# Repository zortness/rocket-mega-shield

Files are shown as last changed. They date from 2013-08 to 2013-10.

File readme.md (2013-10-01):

Rocket Mega Shield Revision 2
=============================

rendering
rendering
rendering

These are the Eagle files for an Arduino Mega shield with sensors and features needed by aviation and rocketry enthusiasts. 
The board is also designed to be extremely easy to use for any hobbyist application. 

These files are released under the [Creative Commons Attribution-ShareAlike](http://creativecommons.org/licenses/by-sa/3.0/) license. 
You're free to use and modify them for any purpose, including commercial.

These files make use of footprints taken from the [Adafruit Eagle Library](https://github.com/adafruit/Adafruit-Eagle-Library) 
and [Sparkfun Eagle Libraries](https://github.com/sparkfun/SparkFun-Eagle-Libraries). 

My library of modified parts is [available here](https://github.com/zortness/zort-eagle-library).

Concept
--------
This shield is geared toward aviation purposes, specifically rocketry. The board itself does not dictate how it is used.
It can also be used for things like planes, boats, cars, or robotics, though this might be overkill for those purposes.

Features
--------
* Supports 5V and 3.3V boards (Mega or Due)
* Supports MicroSD cards that can operate in SPI mode
* Supports all XBee models, using UART Serial for communication
* -- User selectable XBee on UART0 or UART1 via switch
* -- Tie-down holes included in layout
* 10Hz GPS tied to UART2
* -- External GPS Antenna u.FL connector
* High Sensitivity BMP180 Altimeter (barometric pressure and temperature)
* Full 9-degrees-of-freedom capabilities
* -- 3-Axis 16G accelerometer and magnometer (LSM303DLHCTR)
* -- 3-Axis 8-gauss gyroscope (L3GD20TR)
* 3-Axis 200G accelerometer for high-force calculations (ADXL377)
* External reverse-polarity-protected power supply via JST2 connector
* -- Will also power the Arduino
* -- Can also be powered by the Arduino over USB
* -- Up to 18V
* Input voltage measuring at ~1:6 scale
* 4x high-amp MOSFETs with continuity detection
* -- Designed for rocket deployment pyrotechnics
* Automatic level-shifting for sensors (up to 5V)
* Buzzer for making loud noises
* -- MOSFET controlled, attached to PWM pin 8
* Lots of pretty flashing lights

See the [Bill of Materials](https://github.com/zortness/rocket-mega-shield/blob/master/bom.md)
and [parts manifest](https://github.com/zortness/rocket-mega-shield/blob/master/manifest.txt)
for more information.

Versions
--------
* RocketMega Revision 2.1 - Third prototype, only pin and routing changes from R2 for Due compatability
* RocketMega Revision 2 - Second prototype board, intended for wider production, August 2013
* RocketDuino Revision 1 - Initial prototype board, June 2013 

Prototype Images
----------------
Revision 2

R2

Revision 1

R1_a
R1_b

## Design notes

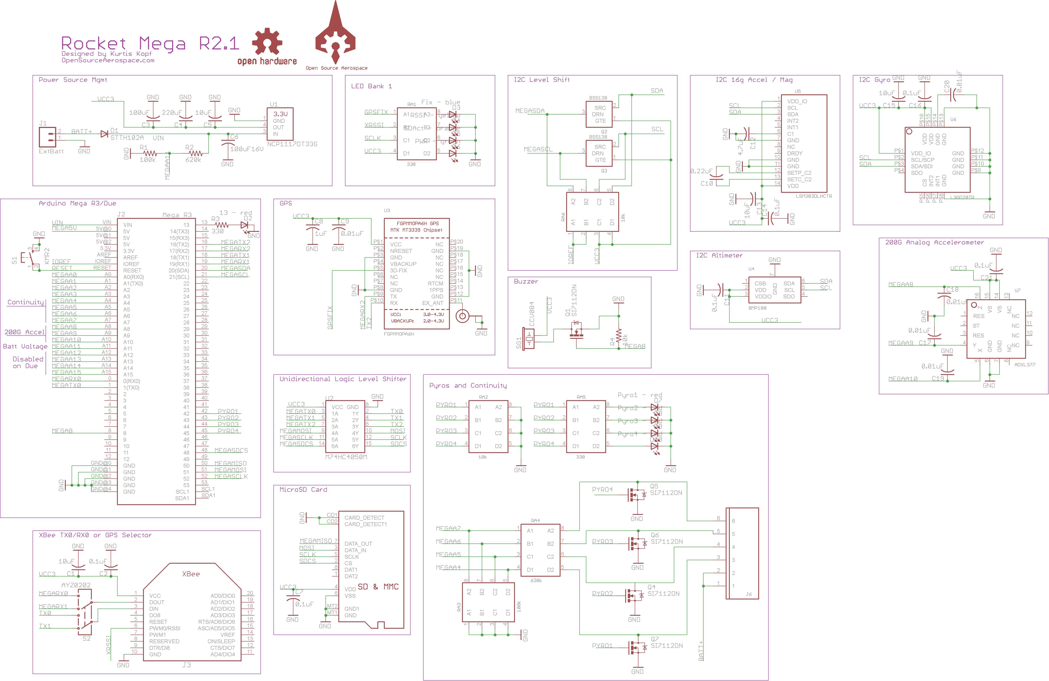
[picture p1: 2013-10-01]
render/rev2.1/schematic.png

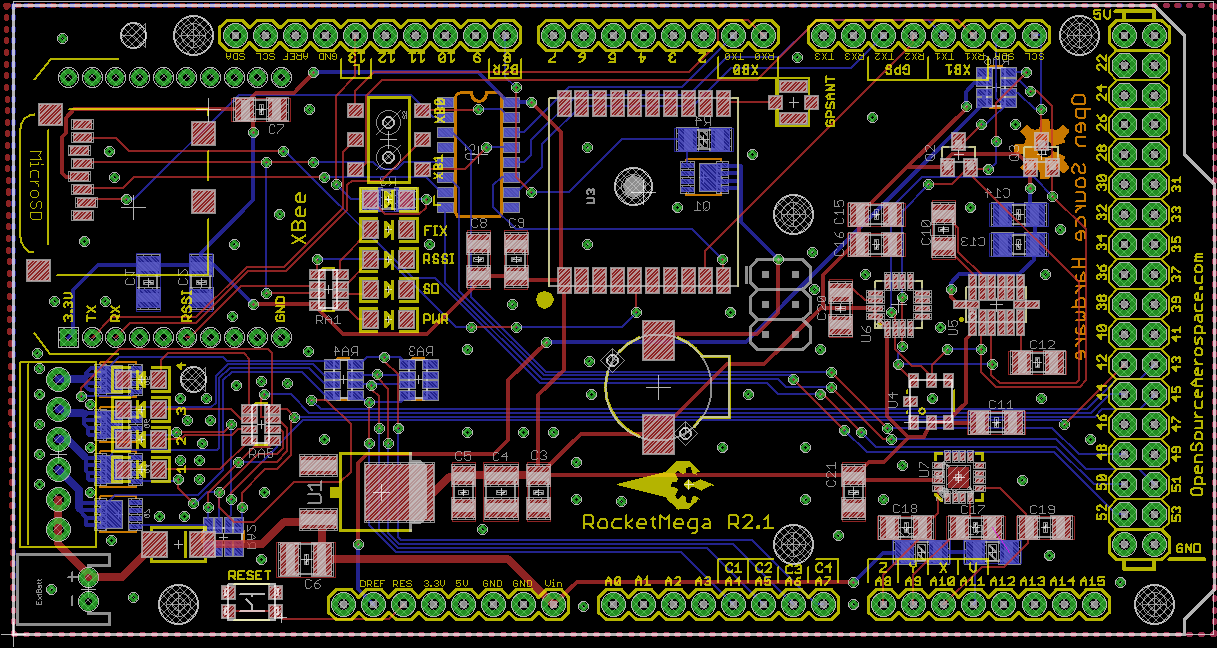
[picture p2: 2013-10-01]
render/rev2.1/board.png

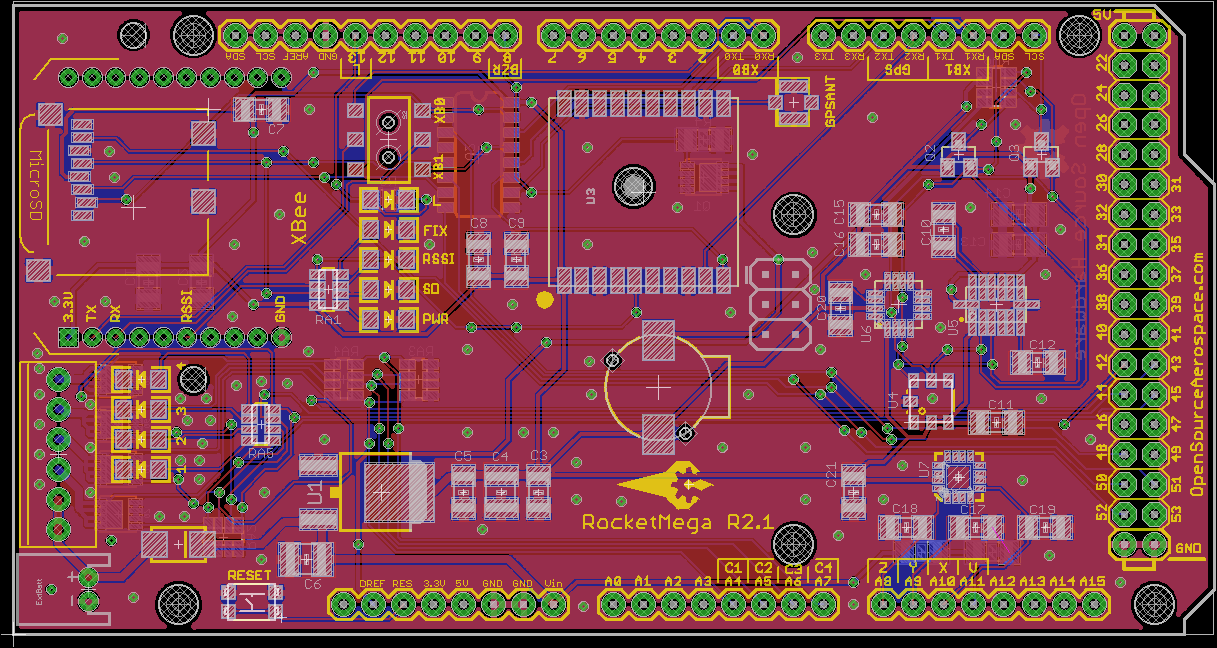
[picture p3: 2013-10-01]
render/rev2.1/board_fill.png

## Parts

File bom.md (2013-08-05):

Bill of materials Revision 2
============================

PCB
-------------------
* 1x RocketMega R2, fab'd by OSHPark: *$16.77*

Integrated Circuits
-------------------
* [3.3V Regulator](http://www.digikey.com/product-detail/en/NCP1117DT33G/NCP1117DT33GOS-ND/1483318): *$0.48*
* [16G Accelerometer / Magnometer LSM303DLHC](http://www.digikey.com/product-detail/en/LSM303DLHCTR/497-11918-1-ND/2757636): *$5.02*
* [200G Accelerometer ADXL-377](http://www.digikey.com/product-detail/en/ADXL377BCPZ-RL7/ADXL377BCPZ-RL7CT-ND/3678489): *$11.12*
* [3-axis Gyro L3GD20](http://www.digikey.com/product-detail/en/L3GD20TR/497-12081-1-ND/2793125): *$6.95*
* [66 channel 10Hz GPS FGPMMOPA6H](http://www.adafruit.com/products/790): *$29.95*
* [BSS138 FET](http://www.digikey.com/product-detail/en/BSS138/BSS138CT-ND/244294): *$0.22* (x2 = *$0.66*)
* [Hex Buffer HC4050](http://www.digikey.com/product-detail/en/M74HC4050RM13TR/497-1844-1-ND/592147): *$0.55*
* [BMP180 Altimeter](http://www.digikey.com/product-detail/en/BMP180/828-1027-1-ND/2688260) *$4.80*
* [SI7112DN N-Channel MOSFET](http://www.digikey.com/product-detail/en/SI7112DN-T1-GE3/SI7112DN-T1-GE3CT-ND/1995641): *$1.59* (x5 = *$7.95*)

*Total:* 13 pieces **$67.48**

Diodes
-----------------
* [STTH102A Diode](http://www.digikey.com/product-detail/en/STTH102A/497-2500-1-ND/603882): *$0.49*
* [1206 LED](http://www.digikey.com/product-detail/en/LTST-C150GKT/160-1169-1-ND/269241): *$0.34* (x9 = *$3.06*) (various colors)

*Total:* 9 pieces, **$3.55**

Passives
-----------------
**Resistors:**
* [330 Ohm Resistor](http://www.digikey.com/product-detail/en/CRCW1206330RJNEA/541-330ECT-ND/1181303): *$0.094*
* [10k Ohm Resistor](http://www.digikey.com/product-detail/en/CRCW120610K0JNEA/541-10KECT-ND/1181339): *$0.094*
* [100k Ohm Resistor](http://www.digikey.com/product-detail/en/CRCW1206110KJNEA/541-110KECT-ND/1181364): *$0.094*
* [620k Ohm Resistor](http://www.digikey.com/product-detail/en/CRCW1206620KJNEA/541-620KECT-ND/1181382): *$0.094*
* [330 Ohm x4 Resistor Array](http://www.digikey.com/product-detail/en/CRA06S083330RJTA/CRA6S8330CT-ND/1285912): *$0.093* (x2 = *$0.186*)
* [10k Ohm x4 Resistor Array](http://www.digikey.com/product-detail/en/CRA06S08310K0JTA/CRA6S810KCT-ND/1285853): *$0.093* (x2 = *$0.186*)
* [100k Ohm x4 Resistor Array](http://www.digikey.com/product-detail/en/CRA06S083110KJTA/CRA6S8110KCT-ND/1285855): *$0.093*
* [620k Ohm x4 Resistor Array](http://www.digikey.com/product-detail/en/CRA06S083620KJTA/CRA6S8620KCT-ND/1285947): *$0.093*

*Total:* 8 pieces, **$0.934**

**Capacitors:**
* [100uF 16V](http://www.digikey.com/product-detail/en/EMK325ABJ107MM-T/587-3152-1-ND/2774765): *$2.25*
* [220uF](http://www.digikey.com/product-detail/en/CL32A227MQVNNNE/1276-3375-1-ND/3891461): *$1.65*
* [100uF](http://www.digikey.com/product-detail/en/C3216X5R0J107M160AB/445-6008-1-ND/2444049): *$1.10*
* [10uF](http://www.digikey.com/product-detail/en/C3216X5R0J106K%2F1.60/445-1388-1-ND/567613): *$0.24* (x4 = *$0.96*)
* [4.7uF](http://www.digikey.com/product-detail/en/C3216X7R1C475K085AB/445-14795-1-ND/3956461): *$0.28*
* [1uF](http://www.digikey.com/product-detail/en/C3216X7R1E105M085AA/445-4024-1-ND/1965670): *$0.20*
* [0.22uF](http://www.digikey.com/product-detail/en/C3216X7R1H224K115AA/445-1379-1-ND/567629): *$0.22*
* [0.1uF](http://www.digikey.com/product-detail/en/C3216X7R2A104K160AA/445-1377-1-ND/567625): *$0.26* (x6 = *$1.56*)
* [0.01uF](http://www.digikey.com/product-detail/en/C3216X5R2J103K115AA/445-14727-1-ND/3956393): *$0.26* (x5 = *$1.30*)

*Total:* 21 pieces, **$9.76**

Electromechanical
-----------------
* [DPDT Switch](http://www.digikey.com/product-detail/en/EG1390A/EG4632CT-ND/1950621): *$0.58*
* [JST-2 connector](http://www.digikey.com/product-detail/en/S2B-XH-A(LF\)(SN\)/455-2257-ND/1651055): *$0.16*
* [Momentary Switch SMD](http://www.digikey.com/product-detail/en/KMR231NG%20LFS/CKN10246CT-ND/2176497): *$0.55*
* [6-port terminal block](http://www.digikey.com/product-detail/en/282834-6/A98337-ND/1153267): *$2.94*
* [MicroSD Socket](http://www.digikey.com/product-detail/en/693071010811/732-3819-1-ND/3124603): *$2.38*
* [Xbee socket](http://www.digikey.com/product-detail/en/NPPN101BFCN-RC/S5751-10-ND/804812): *$1.11* (x2 = *$2.22*)
* [u.FL antenna connector](http://www.digikey.com/product-detail/en/RECE-20279-001E-01/931-1107-1-ND/2332746): *$1.85*
* [CCV084 Buzzer](http://www.digikey.com/product-detail/en/CCV-084B16/102-1265-1-ND/610973): *$2.96*

*Total:* 8 pieces, **$13.64**

Board Build Cost
----------------
about **$113** (plus shipping, solder, equipment, etc.)

Additional items
----------------
* [XBee Pro S3B](http://www.mouser.com/ProductDetail/Digi-International/XBP9B-XCUT-001/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): *$39.00* (x2)
* [Arduino Mega R3](http://www.mouser.com/ProductDetail/Arduino/A000067/?qs=sGAEpiMZZMt0re6d%252b2Rx9v%252bc%252bQEIaOW9): *$45.95*
* [u.FL antenna](http://www.amazon.com/Mini-Antenna-RP-SMA-Bulkhead-Pigtail/dp/B007XVHQ9M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): *$7.75* (x2)
* [XBee USB Adapter](http://www.amazon.com/SainSmart-Adapter-Arduino-Mega2560-Duemilanove/dp/B0085J99CI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): *$15.00*
* 1-2GB MicroSD card: *$5.00*
* 7.4 or higher LiPo battery: about *$7.00*
* laptop with a USB port: ??

Full Setup Cost
---------------
about **$275**

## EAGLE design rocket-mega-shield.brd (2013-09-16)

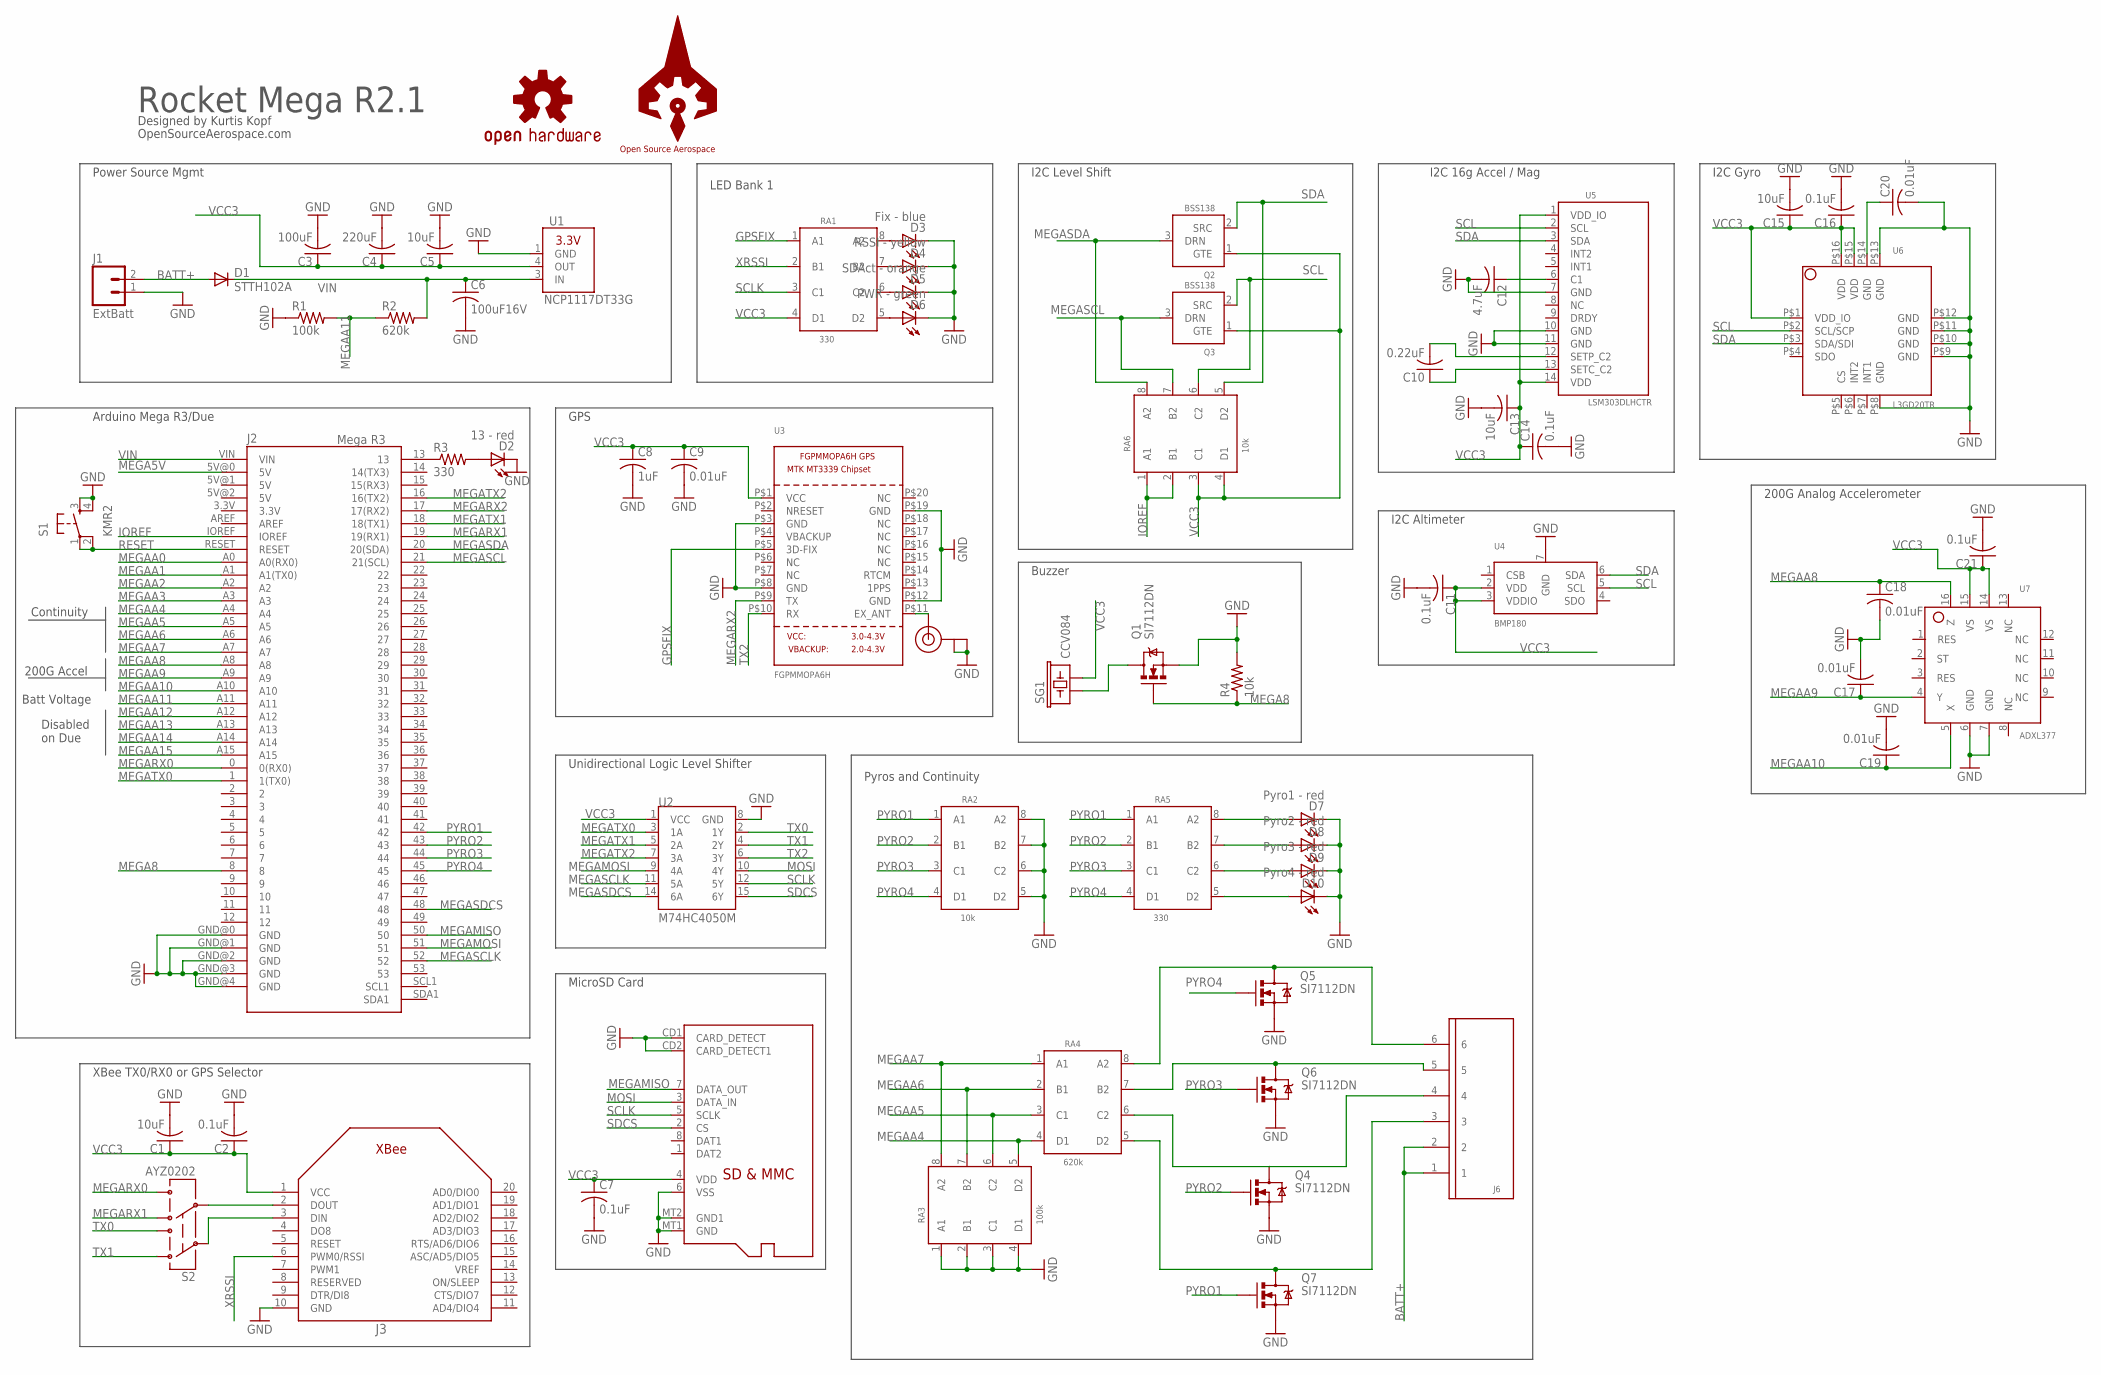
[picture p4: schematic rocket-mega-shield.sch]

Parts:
C1, C5, C13, C15: 10uF; C1206
C2, C7, C11, C14, C16, C21: 0.1uF; C1206
C3: 100uF; C1206
C4: 220uF; C1210
C6: 100uF16V; C1210
C8: 1uF; C1206
C9, C17, C18, C19, C20: 0.01uF; C1206
C10: 0.22uF; C1206
C12: 4.7uF; C1206
D1: STTH102A; SMA-DIODE_ALT
D2: 13 - red; LED-1206
D3: Fix - blue; LED-1206
D4: RSSI - yellow; LED-1206
D5: SDAct - orange; LED-1206
D6: PWR - green; LED-1206
D7: Pyro1 - red; LED-1206
D8: Pyro2 - red; LED-1206
D9: Pyro3 - red; LED-1206
D10: Pyro4 - red; LED-1206
J1: ExtBatt; JST-2-PTH-NS
J2: Mega R3; ARDUINO_MEGA
J3: XBEE
J4: MICROSD
J5: U.FL
J6: 1X6TERMINALBLOCK
LOGO1: OSHW-LOGOM; OSHW-LOGO-M
Q1, Q4, Q5, Q6, Q7: SI7112DN; POWERPAK1212-8
Q2, Q3: BSS138; SOT23
R1: 100k; R1206
R2: 620k; R1206
R3: 330; R1206
R4: 10k; R1206
RA1, RA5: 330; 1206X4RESISTORARRAY
RA2, RA6: 10k; 1206X4RESISTORARRAY
RA3: 100k; 1206X4RESISTORARRAY
RA4: 620k; 1206X4RESISTORARRAY
S1: KMR2; TACTILE_KMR2
S2: AYZ0202
SG1: CCV084; BUZZER-CCV
U1: NCP1117DT33G; DPAK
U2: M74HC4050M; SO016
U3: FGPMMOPA6H
U4: BMP180
U5: LSM303DLHCTR; LGA14
U6: L3GD20TR; LGA16-4X4
U7: ADXL377; LFCSP-16
U$1: OSAEROSPACEVECTOR; OSAEROSPACE_V

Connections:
BATT+: D1.A, J1.2, J6.1, J6.2
GND: C1.2, C2.2, C3.2, C4.2, C5.2, C6.2, C7.2, C8.2, C9.2, C11.2, C12.2, C13.2, C14.2, C15.2, C16.2, C17.2, C18.2, C19.2, C20.2, C21.2, D2.C, D3.C, D4.C, D5.C, D6.C, D7.C, D8.C, D9.C, D10.C, J1.1, J2.GND@0 (GND), J2.GND@1 (GND), J2.GND@2 (GND), J2.GND@3 (GND), J2.GND@4 (GND), J3.10 (GND), J4.6 (VSS), J4.CD1 (CARD_DETECT), J4.CD2 (CARD_DETECT1), J4.MT1 (GND), J4.MT2 (GND1), J5.P$1 (GND), J5.P$2 (GND), Q1.S1 (S), Q1.S2 (S), Q1.S3 (S), Q4.S1 (S), Q4.S2 (S), Q4.S3 (S), Q5.S1 (S), Q5.S2 (S), Q5.S3 (S), Q6.S1 (S), Q6.S2 (S), Q6.S3 (S), Q7.S1 (S), Q7.S2 (S), Q7.S3 (S), R1.1, R4.2, RA2.5 (D2), RA2.6 (C2), RA2.7 (B2), RA2.8 (A2), RA3.1 (A1), RA3.2 (B1), RA3.3 (C1), RA3.4 (D1), S1.3, S1.4, U1.1 (GND), U2.8 (GND), U3.P$3 (GND), U3.P$8 (GND), U3.P$12 (GND), U3.P$19 (GND), U4.7 (GND), U5.7 (GND), U5.10 (GND), U5.11 (GND), U6.P$8 (GND), U6.P$9 (GND), U6.P$10 (GND), U6.P$11 (GND), U6.P$12 (GND), U6.P$13 (GND), U7.6 (GND), U7.7 (GND)
GPSFIX: RA1.1 (A1), U3.P$5 (3D-FIX)
IOREF: J2.IOREF, RA6.1 (A1), RA6.2 (B1)
MEGA5V: J2.5V@0 (5V)
MEGA8: J2.8, Q1.G, R4.1
MEGAA0: J2.A0 (A0(RX0))
MEGAA1: J2.A1 (A1(TX0))
MEGAA2: J2.A2
MEGAA3: J2.A3
MEGAA4: J2.A4, RA3.5 (D2), RA4.4 (D1)
MEGAA5: J2.A5, RA3.6 (C2), RA4.3 (C1)
MEGAA6: J2.A6, RA3.7 (B2), RA4.2 (B1)
MEGAA7: J2.A7, RA3.8 (A2), RA4.1 (A1)
MEGAA8: C18.1, J2.A8, U7.16 (Z)
MEGAA9: C17.1, J2.A9, U7.4 (Y)
MEGAA10: C19.1, J2.A10, U7.5 (X)
MEGAA11: J2.A11, R1.2, R2.1
MEGAA12: J2.A12
MEGAA13: J2.A13
MEGAA14: J2.A14
MEGAA15: J2.A15
MEGAMISO: J2.50, J4.7 (DATA_OUT)
MEGAMOSI: J2.51, U2.9 (4A)
MEGARX0: J2.0 (0(RX0)), S2.4 (6)
MEGARX1: J2.19 (19(RX1)), S2.6 (4)
MEGARX2: J2.17 (17(RX2)), U3.P$9 (TX)
MEGASCL: J2.21 (21(SCL)), Q3.3 (DRN), RA6.7 (B2)
MEGASCLK: J2.52, U2.11 (5A)
MEGASDA: J2.20 (20(SDA)), Q2.3 (DRN), RA6.8 (A2)
MEGASDCS: J2.48, U2.14 (6A)
MEGATX0: J2.1 (1(TX0)), U2.3 (1A)
MEGATX1: J2.18 (18(TX1)), U2.5 (2A)
MEGATX2: J2.16 (16(TX2)), U2.7 (3A)
MOSI: J4.3 (DATA_IN), U2.10 (4Y)
unnamed: D6.A, RA1.5 (D2)
unnamed: D5.A, RA1.6 (C2)
unnamed: J6.3, Q7.D1 (D), Q7.D2 (D), Q7.D3 (D), Q7.D4 (D), Q7.DPAD (D), RA4.5 (D2)
unnamed: J6.4, Q4.D1 (D), Q4.D2 (D), Q4.D3 (D), Q4.D4 (D), Q4.DPAD (D), RA4.6 (C2)
unnamed: C10.2, U5.12 (SETP_C2)
unnamed: C10.1, U5.13 (SETC_C2)
unnamed: C12.1, U5.6 (C1)
unnamed: C20.1, U6.P$14 (GND)
unnamed: J2.13, R3.1
unnamed: J5.P$3 (SIGNAL), U3.P$11 (EX_ANT)
unnamed: D4.A, RA1.7 (B2)
unnamed: D3.A, RA1.8 (A2)
unnamed: Q1.D1 (D), Q1.D2 (D), Q1.D3 (D), Q1.D4 (D), Q1.DPAD (D), SG1.+ (1)
unnamed: D2.A, R3.2
unnamed: D10.A, RA5.5 (D2)
unnamed: D9.A, RA5.6 (C2)
unnamed: D8.A, RA5.7 (B2)
unnamed: D7.A, RA5.8 (A2)
unnamed: J3.2 (DOUT), S2.5
unnamed: J3.3 (DIN), S2.2
unnamed: J6.6, Q5.D1 (D), Q5.D2 (D), Q5.D3 (D), Q5.D4 (D), Q5.DPAD (D), RA4.8 (A2)
unnamed: J6.5, Q6.D1 (D), Q6.D2 (D), Q6.D3 (D), Q6.D4 (D), Q6.DPAD (D), RA4.7 (B2)
PYRO1: J2.42, Q7.G, RA2.1 (A1), RA5.1 (A1)
PYRO2: J2.43, Q4.G, RA2.2 (B1), RA5.2 (B1)
PYRO3: J2.44, Q6.G, RA2.3 (C1), RA5.3 (C1)
PYRO4: J2.45, Q5.G, RA2.4 (D1), RA5.4 (D1)
RESET: J2.RESET, S1.1, S1.2
SCL: Q3.2 (SRC), RA6.6 (C2), U4.5 (SCL), U5.2 (SCL), U6.P$2 (SCL/SCP)
SCLK: J4.5 (SCLK), RA1.3 (C1), U2.12 (5Y)
SDA: Q2.2 (SRC), RA6.5 (D2), U4.6 (SDA), U5.3 (SDA), U6.P$3 (SDA/SDI)
SDCS: J4.2 (CS), U2.15 (6Y)
TX0: S2.1 (3), U2.2 (1Y)
TX1: S2.3 (1), U2.4 (2Y)
TX2: U2.6 (3Y), U3.P$10 (RX)
VCC3: C1.1, C2.1, C3.1, C4.1, C5.1, C7.1, C8.1, C9.1, C11.1, C13.1, C14.1, C15.1, C16.1, C21.1, J3.1 (VCC), J4.4 (VDD), Q2.1 (GTE), Q3.1 (GTE), RA1.4 (D1), RA6.3 (C1), RA6.4 (D1), SG1.- (2), U1.4 (OUT), U2.1 (VCC), U3.P$1 (VCC), U4.2 (VDD), U4.3 (VDDIO), U5.1 (VDD_IO), U5.14 (VDD), U6.P$1 (VDD_IO), U6.P$15 (VDD), U6.P$16 (VDD), U7.14 (VS), U7.15 (VS)
VIN: C6.1, D1.C, J2.VIN, R2.2, U1.3 (IN)
XRSSI: J3.6 (PWM0/RSSI), RA1.2 (B1)

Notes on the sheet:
Power Source Mgmt
Arduino Mega R3/Due
I2C Level Shift
200G Analog Accelerometer
I2C Altimeter
I2C 16g Accel / Mag
I2C Gyro
GPS
Unidirectional Logic Level Shifter
XBee TX0/RX0 or GPS Selector
MicroSD Card
Pyros and Continuity
Rocket Mega R2.1
LED Bank 1
200G Accel
Continuity
Batt Voltage
Buzzer
Designed by Kurtis Kopf
OpenSourceAerospace.com
Disabled on Due

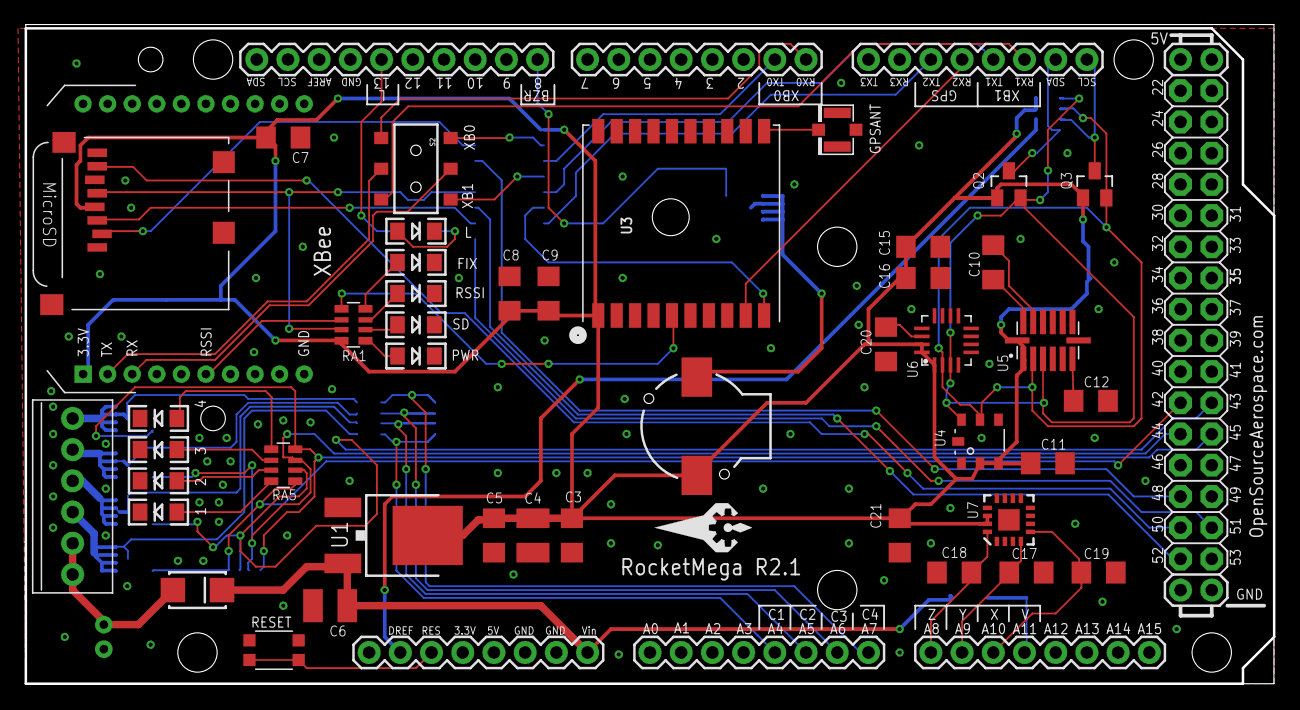
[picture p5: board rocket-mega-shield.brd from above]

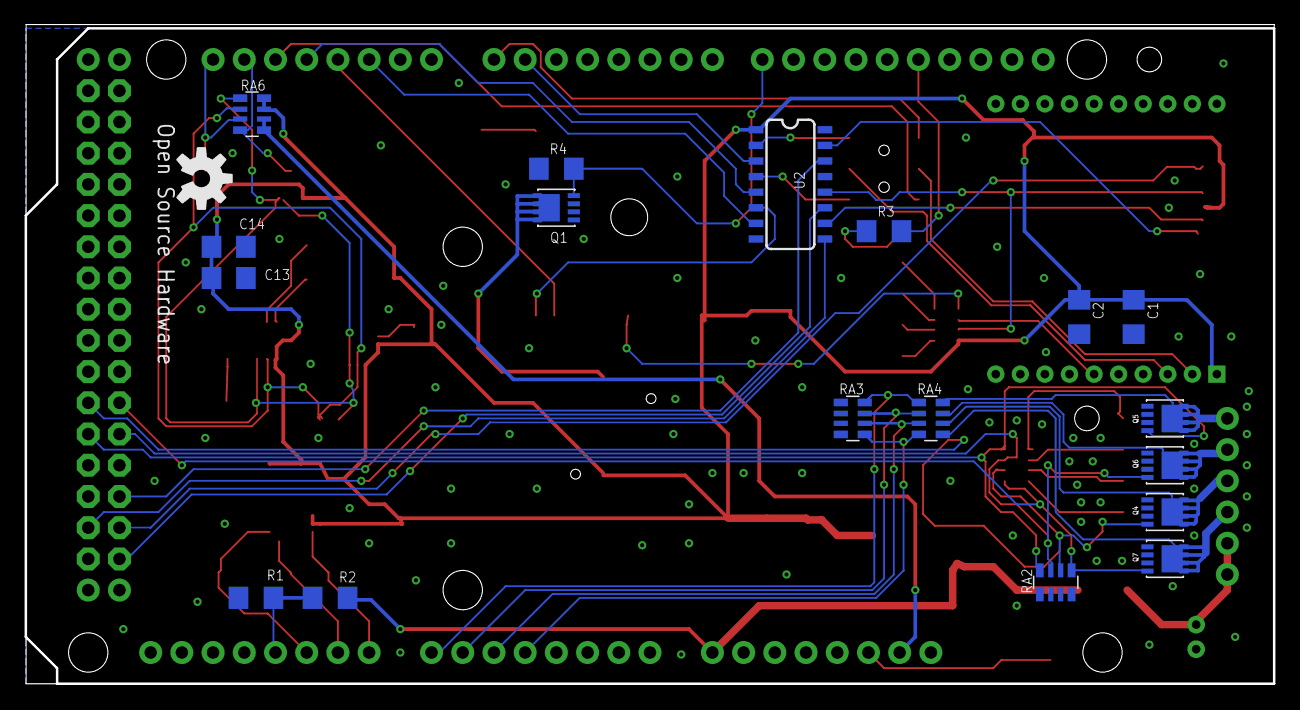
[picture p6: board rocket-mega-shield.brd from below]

Board: 2 copper layers, 101.6 x 53.6 mm, 66 parts (19 on the bottom side), 63 nets.

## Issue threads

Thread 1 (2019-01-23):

Need some ICs for substitution

lilcommieblyat, 2019-01-23:
Hi, zortness! Your project is amazing!
But Some of the ICs are no longer in production or out of stock. Do you have an updated version of the PCB so that some currently-available ICs can be used?

Closed 2019-03-26.

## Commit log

2013-06-20 initial commit, V1 of the board
    [rocket-mega-shield.brd, rocket-mega-shield.sch]
2013-07-05 added bill of materials and costs
2013-07-20 new images added of prototype
2013-07-24 working on revision 2, not done yet
    [rocket-mega-shield.brd, rocket-mega-shield.sch]
2013-07-27 initial schematic with mosfets and continuity checking
    [rocket-mega-shield.brd, rocket-mega-shield.sch]
2013-07-29 working on layout for rev2
    [rocket-mega-shield.brd, rocket-mega-shield.sch]
2013-08-01 mostly done with schematic and layout... still need to add fuse and clean up labeling
    [rocket-mega-shield.brd, rocket-mega-shield.sch]
2013-08-01 fixing goofy extra via
    [rocket-mega-shield.brd]
2013-08-01 working on cleaning up the shield, will have to switch to the BMP180, went through the manifest and bill of materials
    [rocket-mega-shield.brd, rocket-mega-shield.sch]
2013-08-01 fixing line breaks in BOM
2013-08-02 prettying up the BOM
2013-08-02 changed sd card, added holes to die down xb, changed reset switch, renamed all parts to match conventions, various other cleanup, adjusted BOM and manifest
    [rocket-mega-shield.brd, rocket-mega-shield.sch]
2013-08-02 added buzzer on pin 8, moved all analog reads down to second set of pins, A8-A15, updated manifest, bom, and images
    [rocket-mega-shield.brd, rocket-mega-shield.sch]
2013-08-02 forgot to update schematic
2013-08-02 added LED on pin 13, more cleanup, updated BOM
    [rocket-mega-shield.brd, rocket-mega-shield.sch]
2013-08-03 routing and visual cleanup
    [rocket-mega-shield.brd, rocket-mega-shield.sch]
2013-08-03 slight update to labelling and routing around xbee
    [rocket-mega-shield.brd]
2013-08-04 changed out mosfet on speaker for higher amperage, more cleanup
    [rocket-mega-shield.brd, rocket-mega-shield.sch]
2013-08-05 changed mosfet for speaker, added osaerospace logo
    [rocket-mega-shield.brd, rocket-mega-shield.sch]
2013-08-15 changed out xbee to clean up screen printing lines, trimmed working window down to actual board size
    [rocket-mega-shield.brd, rocket-mega-shield.sch]
2013-08-15 cleaning up some power nets, flipped buzzer around for better routing
    [rocket-mega-shield.brd]
2013-09-08 moving pins around to match the Due pin availablility
    [rocket-mega-shield.brd, rocket-mega-shield.sch]
2013-09-16 more cleanup on the 2.1 board
    [rocket-mega-shield.brd, rocket-mega-shield.sch]

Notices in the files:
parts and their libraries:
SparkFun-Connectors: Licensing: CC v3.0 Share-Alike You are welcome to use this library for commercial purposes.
